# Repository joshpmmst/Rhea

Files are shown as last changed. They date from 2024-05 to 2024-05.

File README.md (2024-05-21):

# Rhea: An open-source table tennis ball launcher robot for multiball training

<picture>
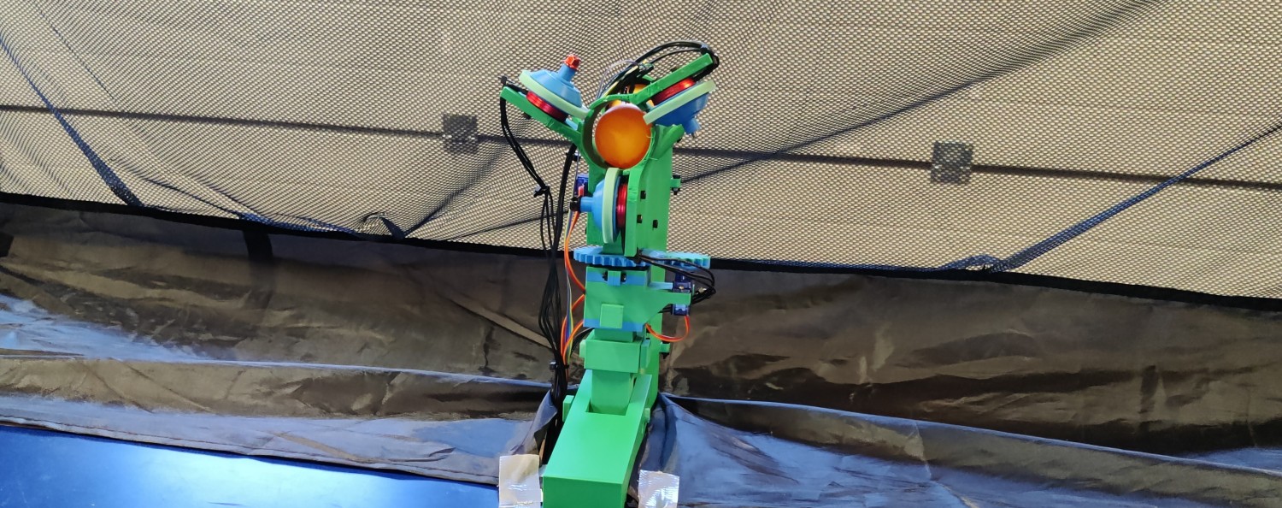
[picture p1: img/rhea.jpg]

</picture>

## About

Rhea is an open-source table tennis ball launcher intended for multiball training.
Rhea is manufacturable with common hobbyist tools and comprises of readily available materials and components.

## Contents
  - [3D printing and assembly instructions](printing-and-assembly)
  - [Bill of Materials](bill-of-materials)
  - [3D models](models)
  - [Firmware](firmware)
  - [User software](software)

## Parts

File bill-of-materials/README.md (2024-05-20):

## Bill of Materials

All prices as of 2024-05-20.

Component | Quantity | Cost (EUR)
---|---|---
TowerPro SG90 | 2 | [4.94](https://nettigo.eu/products/sg90-small-hobby-servo)
Parallax Continuous Rotation Servo #900-00008 | 1 | [18.55](https://www.mouser.ee/ProductDetail/Parallax/900-00008?qs=Ok6sVjDQtqYSeReZa9t%252Bvg%3D%3D)
Racerstar BR2205S 2300KV | 3 | [38.16](https://www.banggood.com/Racerstar-Racing-Edition-2205-BR2205-2300KV-2-4S-Brushless-Motor-Red-for-220-250-RC-Drone-FPV-Racing-p-1065661.html?ID=521309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)
Racerstar MS Series 35A | 3 | [51.00](https://www.ariesrc.gr/en/speed-controller/16240-racerstar-ms-series-35a-esc-blhelis-opto-2-4s-supports-dshot600-for-rc-drone-fpv-racing-multi-rotor.html) (a)
Zhermack Elite Double 22 polysiloxane | 20 ml | [0.76](https://edenta.eu/et/proteesitarvikud/elite-double-22-normal-1-kg-1-kg) (b)
PLA filament | 1115 g | [18.46](https://esun3dstore.com/collections/pla/products/esun-epla-ss-1-75mm-3d-filament-1kg)
DOIT ESP32 DevKit V1 | 1 | [4.73](https://www.aliexpress.com/item/1005005988314674.html)
Vishay TCRT5000 | 2 | [3.96](https://ee.farnell.com/vishay/tcrt5000/sensor-optical-transistor-o-p/dp/1470066)
TIGER Power Supplies TP1024 | 1 | [14.31](https://ee.farnell.com/tiger-power-supplies/tp1024/power-supply-ac-dc-1o-p-5a-12v/dp/4132955)
Wurth Elektronik 694106402002 | 1 | [1.24](https://ee.farnell.com/wurth-elektronik/694101308002/connector-power-entry-jack-2a/dp/2472139)
OKYSTAR OKY3501-1 | 1 | [5.08](https://www.teval.ee/en/shop/product/oky3501-1-converter-step-down-uout-5v-uin-624v-3a-94-26-4x15mm-236530) (c)
Quarter sized protoboard | 1 | [2.02](https://www.aliexpress.com/item/4000372698705.html)
WAGO 221 3-conductor | 3 | [2.07](https://solislux.eu/en/product/221-613-compact-splicing-connectors;-3-conductor-connector;-with-operating-levers;-max-ambient-operating-temp--85-%C2%B0c/)
WAGO 221 5-conductor | 1 | [1.16](https://solislux.eu/en/product/221-615-compact-splicing-connectors;-5-conductor-connector;-with-operating-levers;-max-ambient-operating-temp--85-%C2%B0c/)
470 Ohm resistor | 2 | 0.02 (d)
10k Ohm resistor | 2 | 0.02 (d)
22 AWG four wire ribbon cable | 1 m | [1.28](https://www.aliexpress.com/item/32956565616.htm)
18 AWG wire | 3 m | [2.38](https://ee.farnell.com/pro-power/pp001187/tri-rated-wire-1mm2-black-1m/dp/2528083)
14 AWG wire | 2 m | [3.35](https://ee.farnell.com/pro-power/pp001189/tri-rated-wire-2-5mm2-black-1m/dp/2528085)
10 cm male to female jumper wires | 20 | [0.97](https://www.aliexpress.com/item/4000203371860.html)
15x32x9 metal ball bearing 6002/C3 SKF | 1 | [5.13](https://www.alas-kuul.ee/radiaalkuullaager-6002-c3-skf)
M3 bolts and nuts | 1 | 1.21 (e)
**TOTAL** | | **180.80**

(a) - Can be substitituded with more recent ESCs:
[Simonk 10A](https://www.aliexpress.com/item/1005005032261137.html) (14.58 EUR for 3 pieces).

(b) - Can be substituted, recommended Shore A hardness of 20-25. [Polistep PLS-525](https://polistep.lv/en/two-component-silicone/tproduct/282059541-460415774771-moulding-silicone-on-tin-catalyst-pls-52) (0.36 EUR for 20 ml)

(c) - Can be substituted. [LM2596 DC-DC module](https://www.aliexpress.com/item/1005004904872120.html) (1.57 EUR per piece)

(d) - The resistors were used from a 300 piece kit costing [2.28](https://www.aliexpress.com/item/1005006209050774.html) EUR.

(e) - M3 bolts and nuts were used from a 300 piece kit costing [6.48](https://www.aliexpress.com/item/33022099174.html) EUR. The following lists all M3 bolts and nuts used.

Component | Quantity
---|---
M3x8 bolt | 14
M3x12 bolt | 22
M3x16 bolt | 4
M3x20 bolt | 4
M3 nut | 12

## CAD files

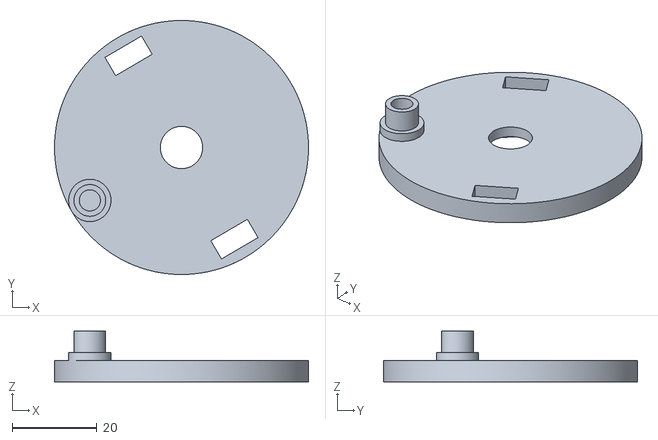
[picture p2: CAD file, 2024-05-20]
models/Ball Pusher/Crank.stl
60.0 x 60.0 x 12.0

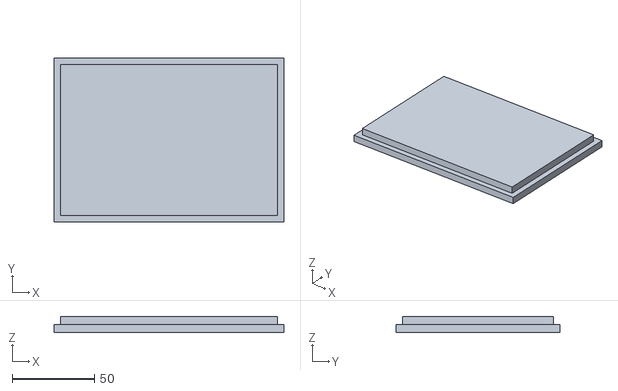
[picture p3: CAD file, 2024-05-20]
models/Enclosure/Enclosure lid.stl
140.0 x 100.0 x 10.0

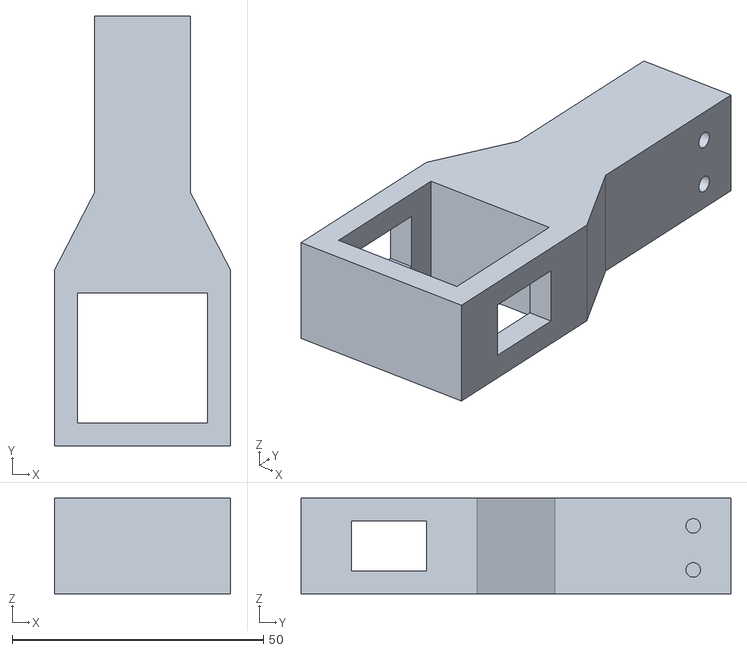
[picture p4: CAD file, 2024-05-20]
models/Fixture/Pusher and Pipe connector.stl
35.0 x 85.5 x 19.0

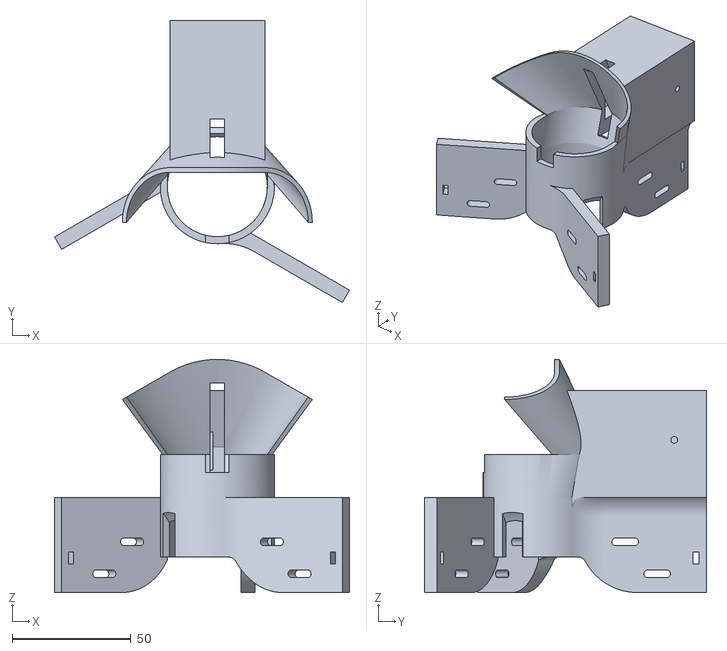
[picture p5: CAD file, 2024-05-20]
models/Launch Unit/Launch Unit.stl
124.0 x 118.6 x 98.0

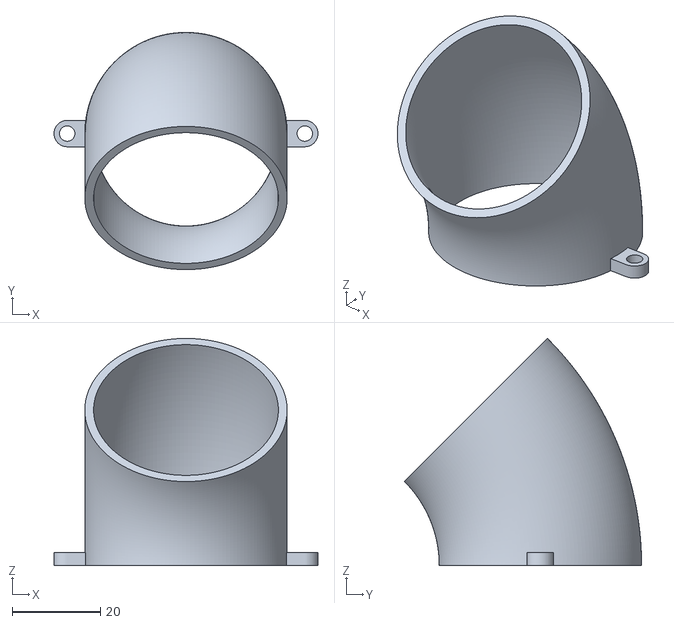
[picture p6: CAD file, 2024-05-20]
models/Pipe/Angled connector pipe 2.stl
60.0 x 53.9 x 51.6

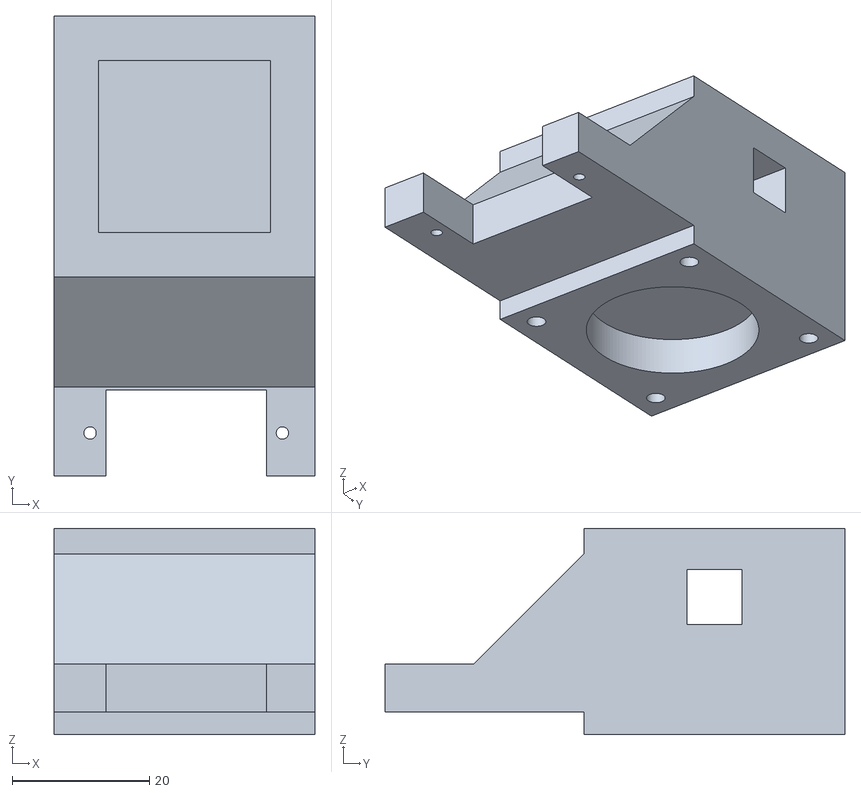
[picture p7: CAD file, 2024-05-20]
models/Pivot Mechanism/Housing.stl
38.0 x 67.0 x 30.0

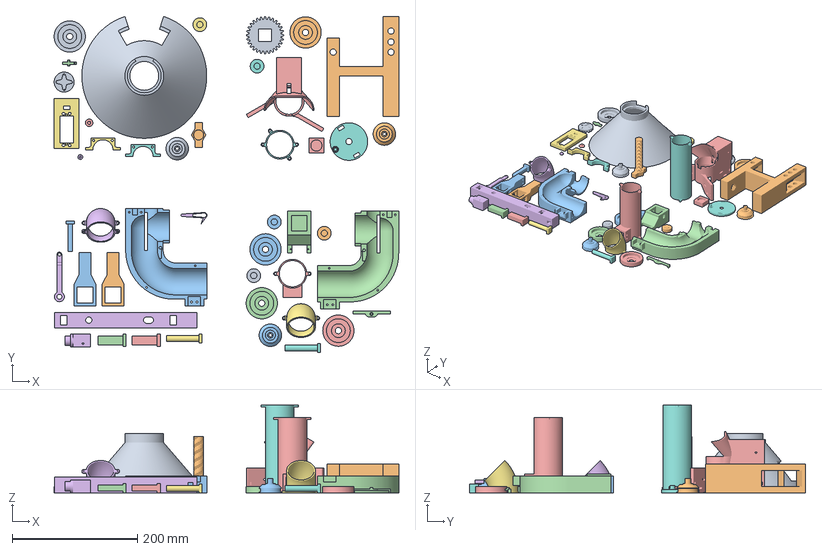
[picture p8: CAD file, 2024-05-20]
models/Plates.3mf
551.2 x 537.2 x 140.0 mm
Funnel.stl
Clamp.stl
Housing 2.stl
Housing 1.stl
Launch Unit.stl
Rod.stl
Parallax servo holder.stl
Crank.stl
Driven gear.stl
Pusher and Pipe connector.stl x 2
Housing.stl
Straight connector pipe top.stl
Angled connector pipe 1.stl
Angled connector pipe 2.stl
Straight connector pipe bottom.stl
Traction wheel mould outer.stl x 5
Connecting rod.stl
Bearing housing.stl x 2
Motor guard.stl x 3
Rectangular dowel.stl x 2
Shaft.stl
Round dowel.stl x 2
Driver gear.stl
Bolt.stl
Square dowel.stl
Piston.stl
Bolt pad.stl
Servo hook.stl
Traction wheel mould inner.stl x 5
Ball stopper.stl
Crank retaining pin.stl
Piston retaining pin.stl

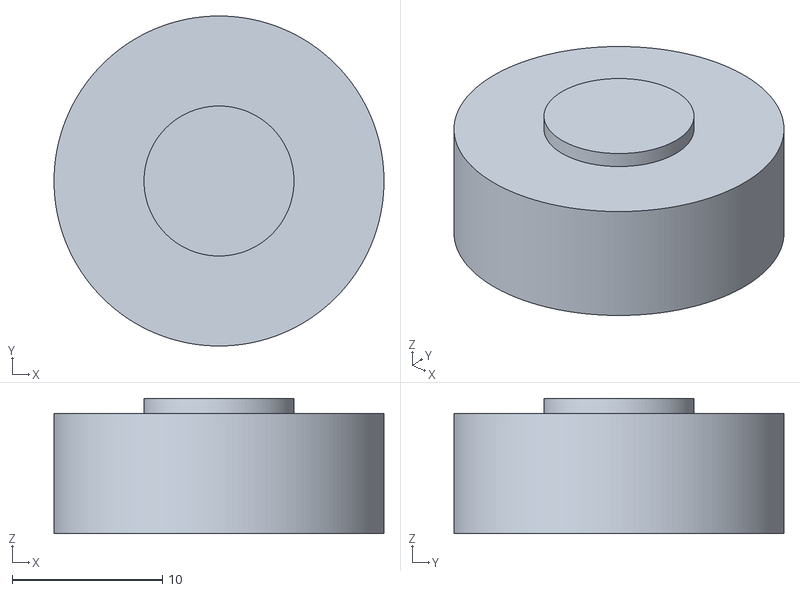
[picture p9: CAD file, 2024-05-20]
models/Traction wheel mould/Traction wheel mould inner.stl
22.0 x 22.0 x 9.00

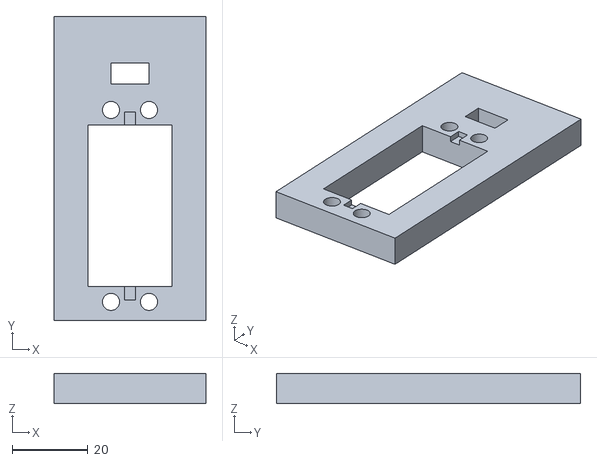
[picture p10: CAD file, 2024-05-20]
models/Ball Pusher/Parallax servo holder.stl
40.0 x 80.0 x 8.00

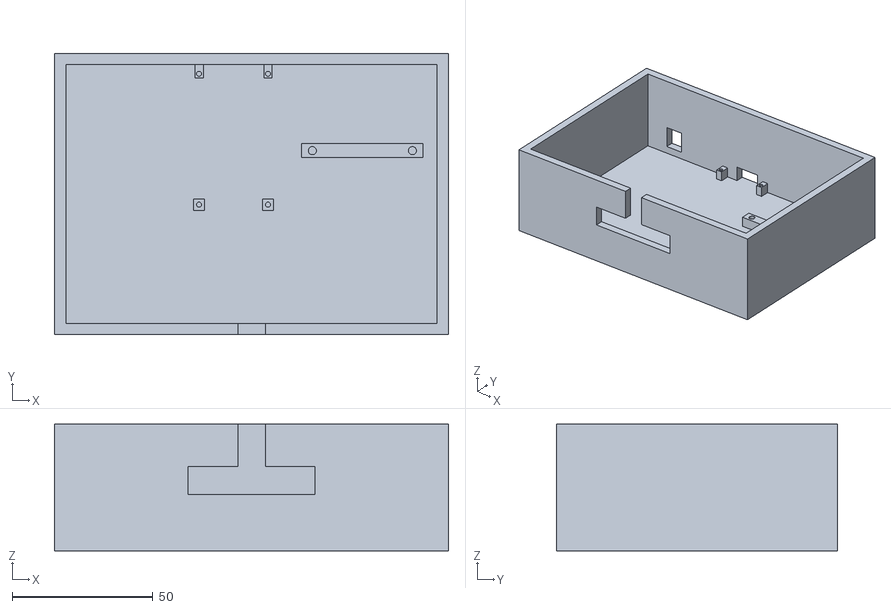
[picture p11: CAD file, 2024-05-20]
models/Enclosure/Enclosure.stl
140.0 x 100.0 x 45.0

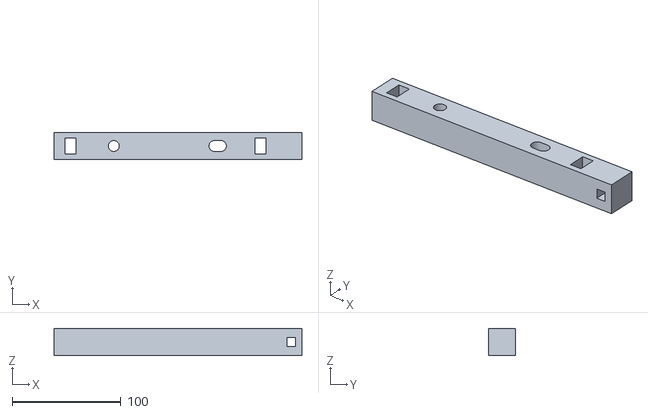
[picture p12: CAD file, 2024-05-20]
models/Fixture/Rod.stl
228.0 x 25.0 x 25.0

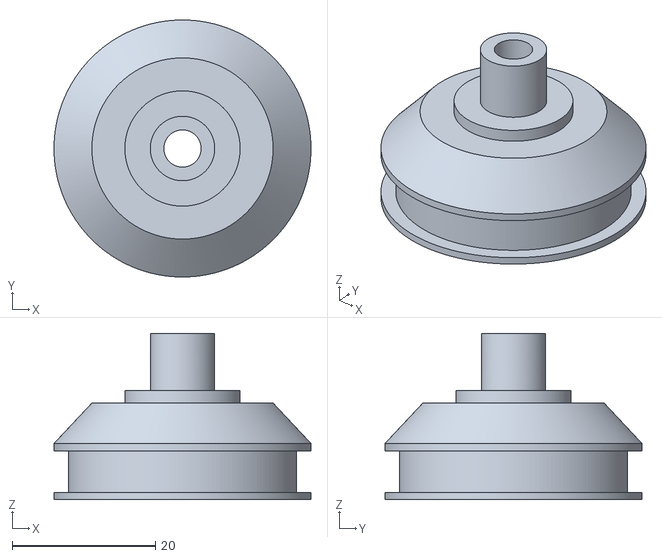
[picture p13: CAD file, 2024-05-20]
models/Launch Unit/Motor guard.stl
35.9 x 35.9 x 23.2

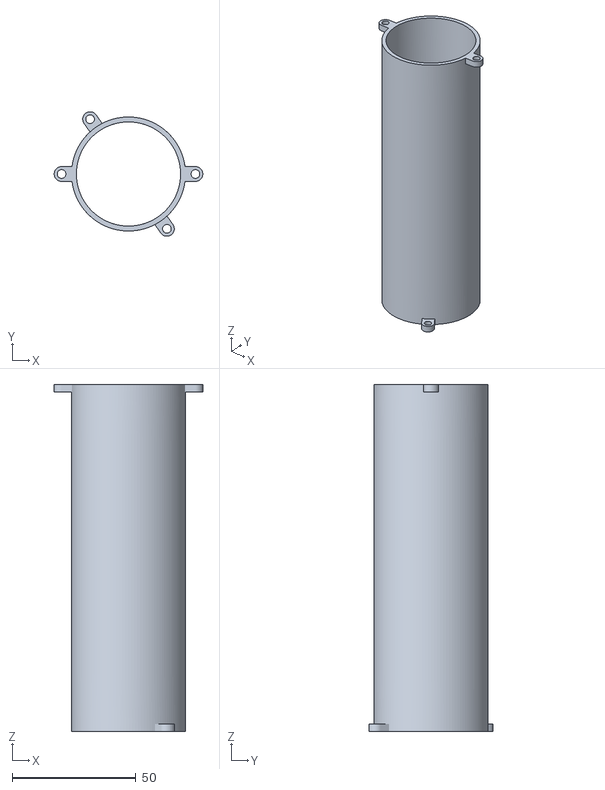
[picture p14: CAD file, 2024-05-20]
models/Pipe/Straight connector pipe bottom.stl
60.0 x 50.2 x 140.0

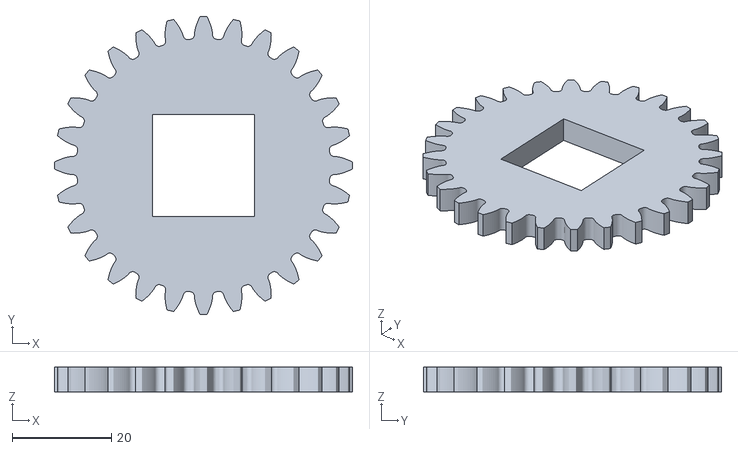
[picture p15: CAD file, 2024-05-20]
models/Pivot Mechanism/Driven gear.stl
60.0 x 60.0 x 5.00

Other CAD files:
models/Traction wheel mould/Traction wheel mould outer.stl
models/Ball Pusher/Piston retaining pin.stl
models/Fixture/Clamp.stl
models/Launch Unit/Servo hook.stl
models/Ball Pusher/Ball stopper.stl
models/Ball Pusher/Connecting rod.stl
models/Ball Pusher/Crank retaining pin.stl
models/Ball Pusher/Funnel.stl
models/Ball Pusher/Housing 1.stl
models/Ball Pusher/Housing 2.stl
models/Ball Pusher/Piston.stl
models/Fixture/Bolt pad.stl
models/Fixture/Bolt.stl
models/Fixture/Rectangular dowel.stl
models/Fixture/Round dowel.stl
models/Fixture/Square dowel.stl
models/Pipe/Angled connector pipe 1.stl
models/Pipe/Straight connector pipe top.stl
models/Pivot Mechanism/Bearing housing.stl
models/Pivot Mechanism/Driver gear.stl
models/Pivot Mechanism/Shaft.stl

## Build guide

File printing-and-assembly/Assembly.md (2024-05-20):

# Assembly instructions

## Ball Pusher

1. Solder four ribbon cable wires to the TCRT5000 sensor and glue it to the `Parallax servo holder`.

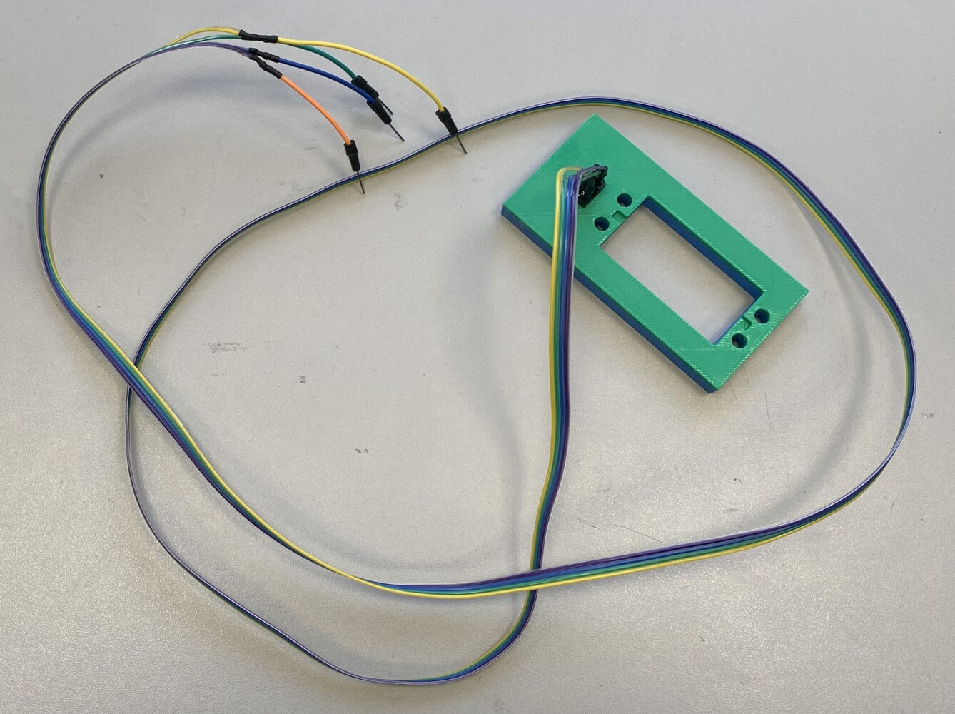
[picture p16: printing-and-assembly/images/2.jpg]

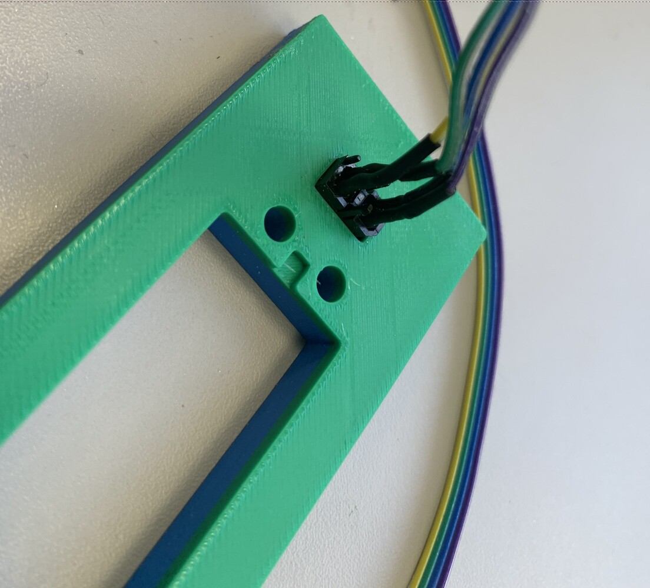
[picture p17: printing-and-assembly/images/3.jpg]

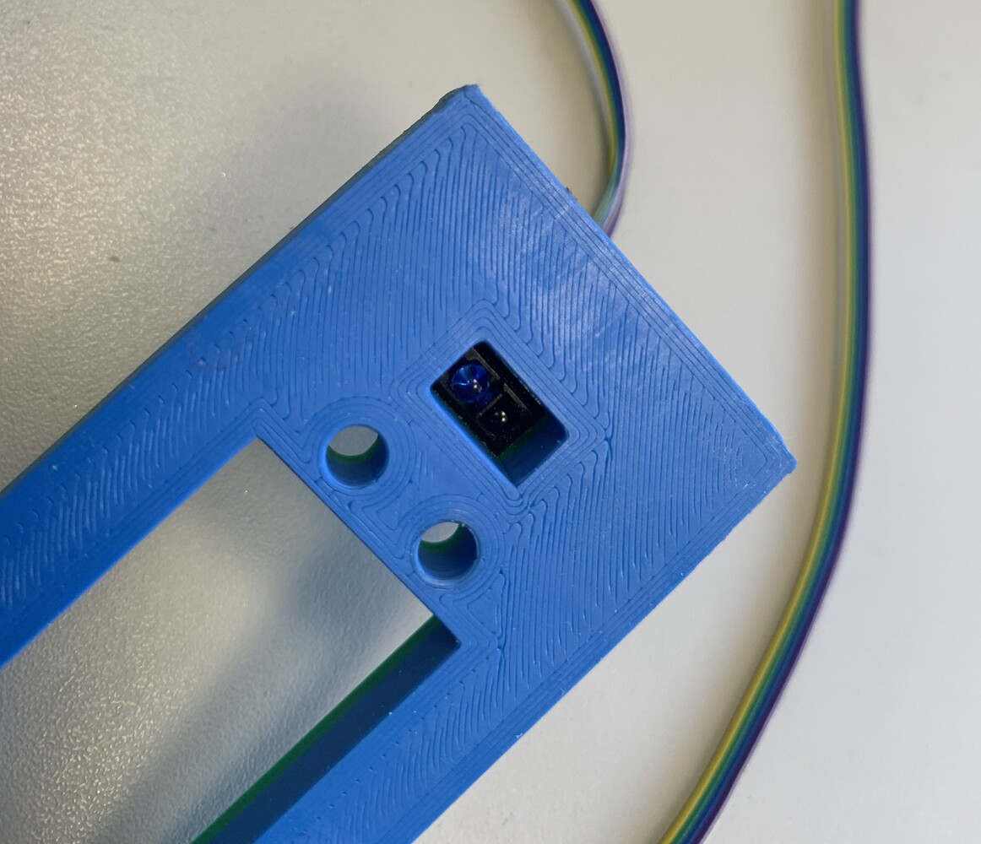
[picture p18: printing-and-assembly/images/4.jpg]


2. Mount the Parallax continuous servomotor to the `Parallax servo holder` using four M3x16 bolts with nuts. Two bolts are sufficient.

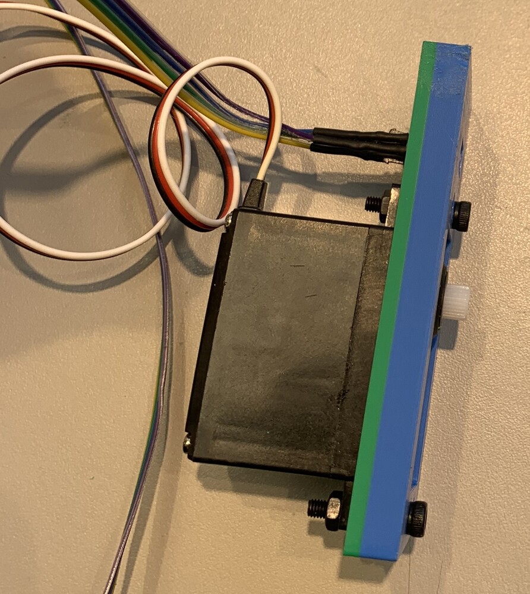
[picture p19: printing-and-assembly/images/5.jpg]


3. Pressure fit the cross-shaped connector provided with the Parallax continous servo into the `Crank`. Use glue if the fit is loose.

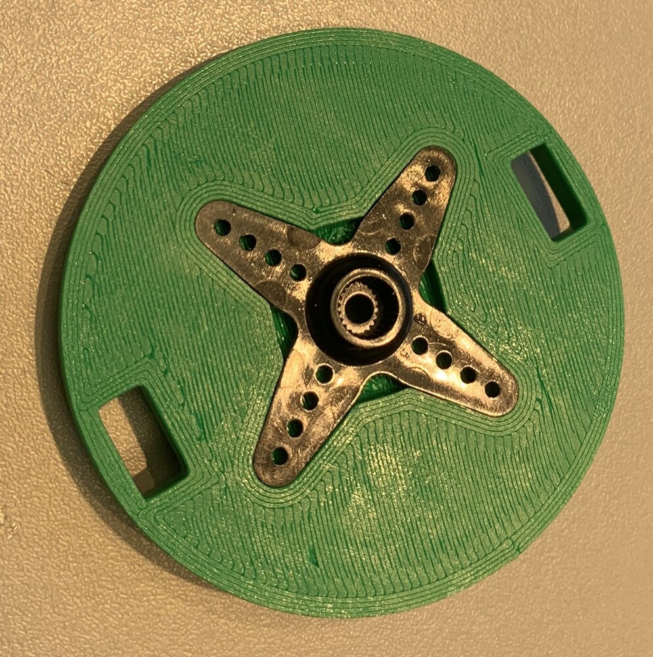
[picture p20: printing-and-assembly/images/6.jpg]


4. Secure the cross connector and the `Crank` to the servomotor using the screw provided with the servomotor.

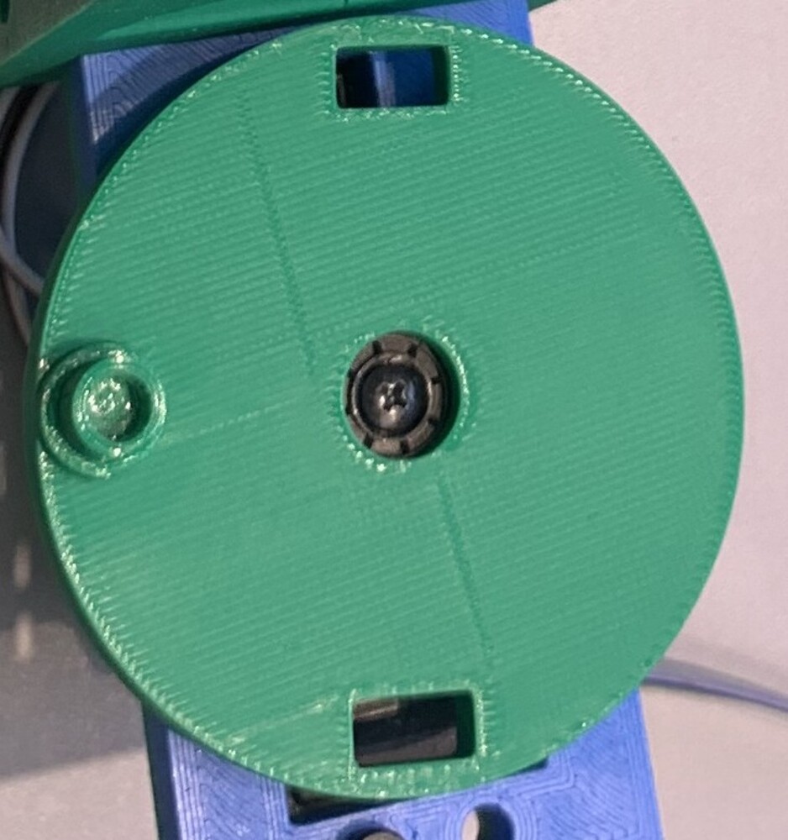
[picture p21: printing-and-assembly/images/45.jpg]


5. Pressure fit the `Parallax servo holder` into `Housing 1`. Place the `Ball stopper` into `Housing 1` as indicated by the red square.

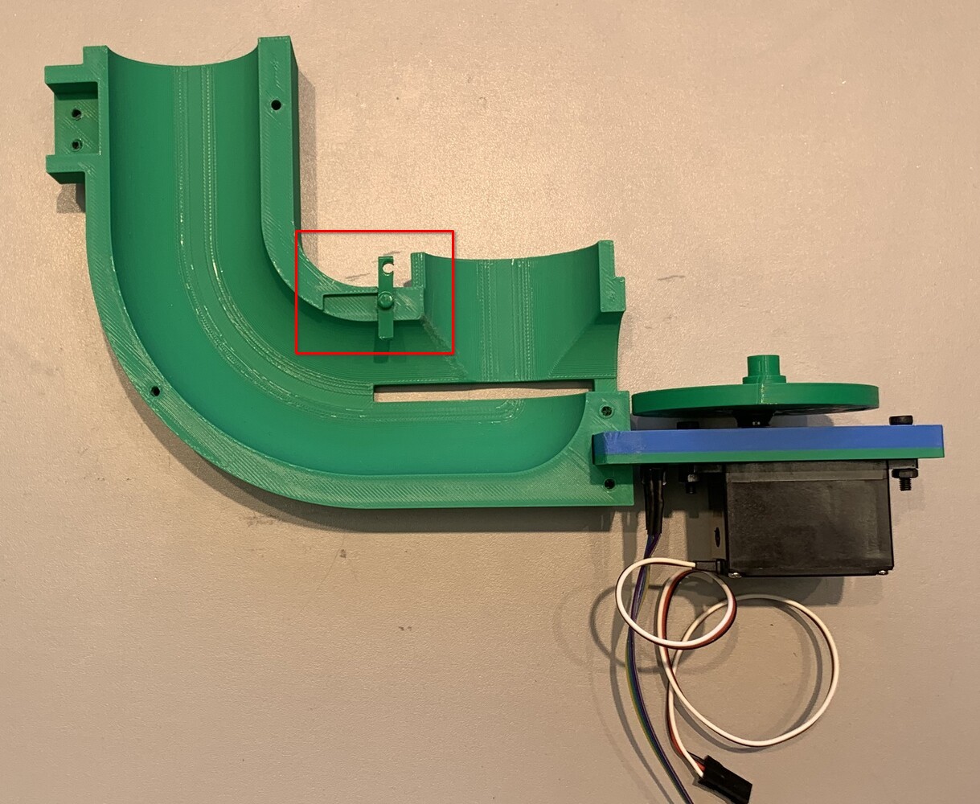
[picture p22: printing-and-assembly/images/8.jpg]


6. Slide the `Piston` sideways into `Housing 1`.

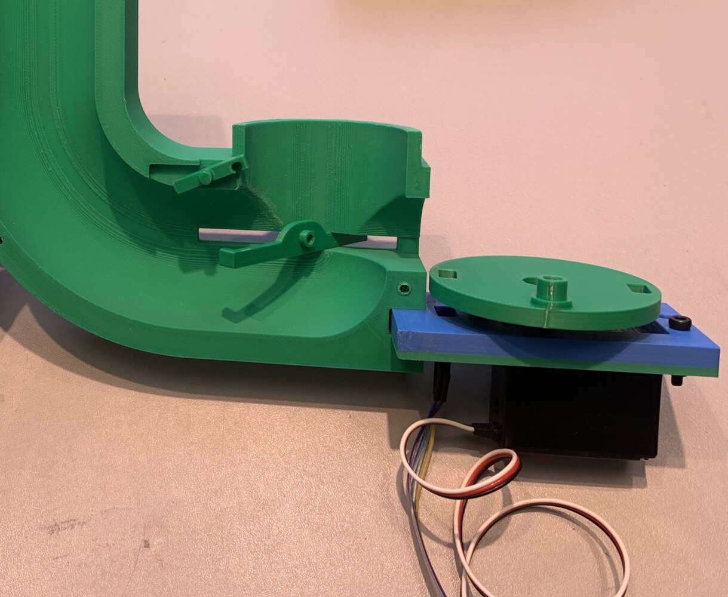
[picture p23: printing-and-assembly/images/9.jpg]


7. Attach `Housing 2` to `Housing 1`.

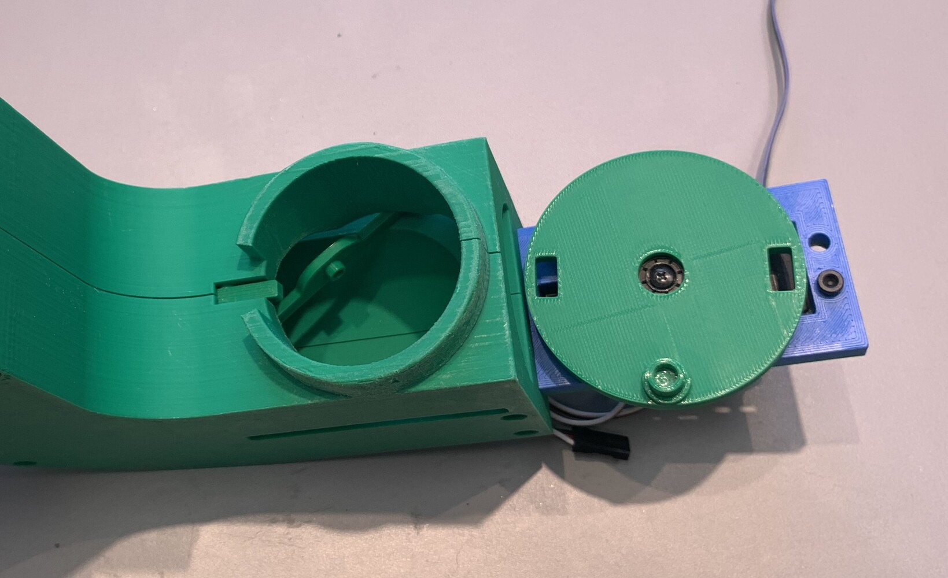
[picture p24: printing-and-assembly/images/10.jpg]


8. Twist the `Piston` counterclockwise so it is parallel to the sliding surface.

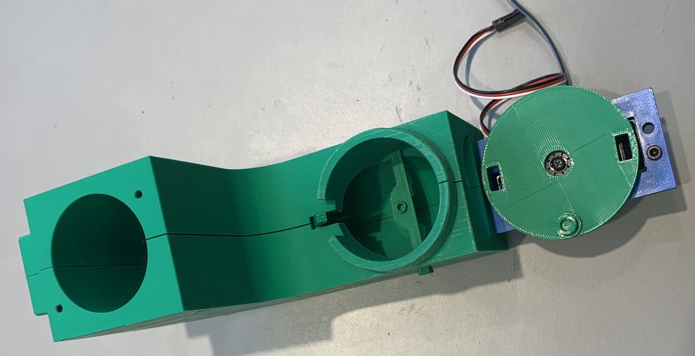
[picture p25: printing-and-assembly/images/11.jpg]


9. Attach the `Connecting rod` to the `Crank` and `Piston`.

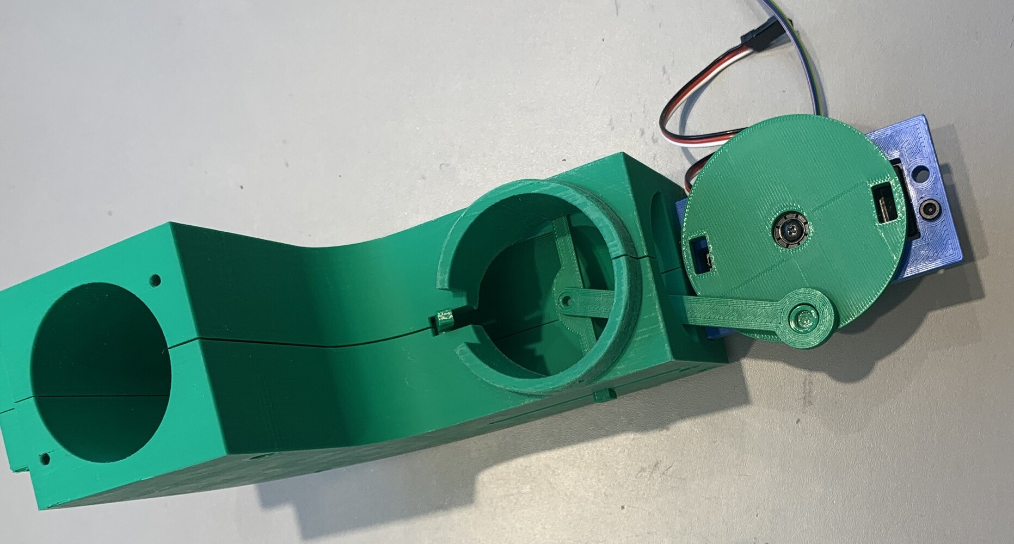
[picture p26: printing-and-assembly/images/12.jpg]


10. Attach the `Crank retaining pin` to the `Crank` and the `Piston retaining pin` to the `Piston`.

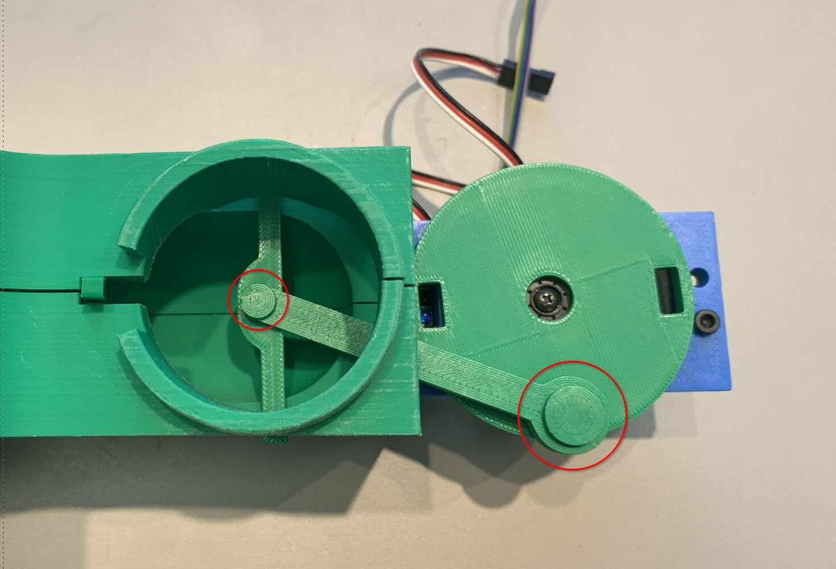
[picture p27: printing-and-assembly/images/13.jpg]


11. Secure `Housing 1` and `Housing 2` together using four M3x20 bolts. Nuts are not required as the holes' inner diameter is smaller inside.

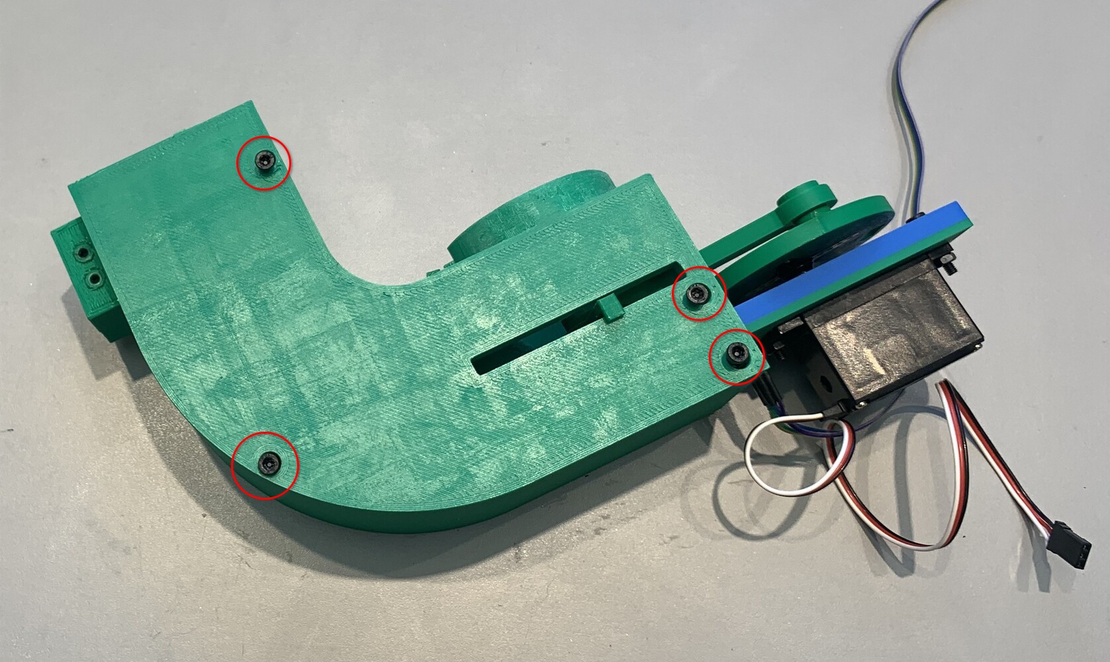
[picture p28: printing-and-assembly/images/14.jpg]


12. Attach a rubber band to hold the `Ball stopper` upright.

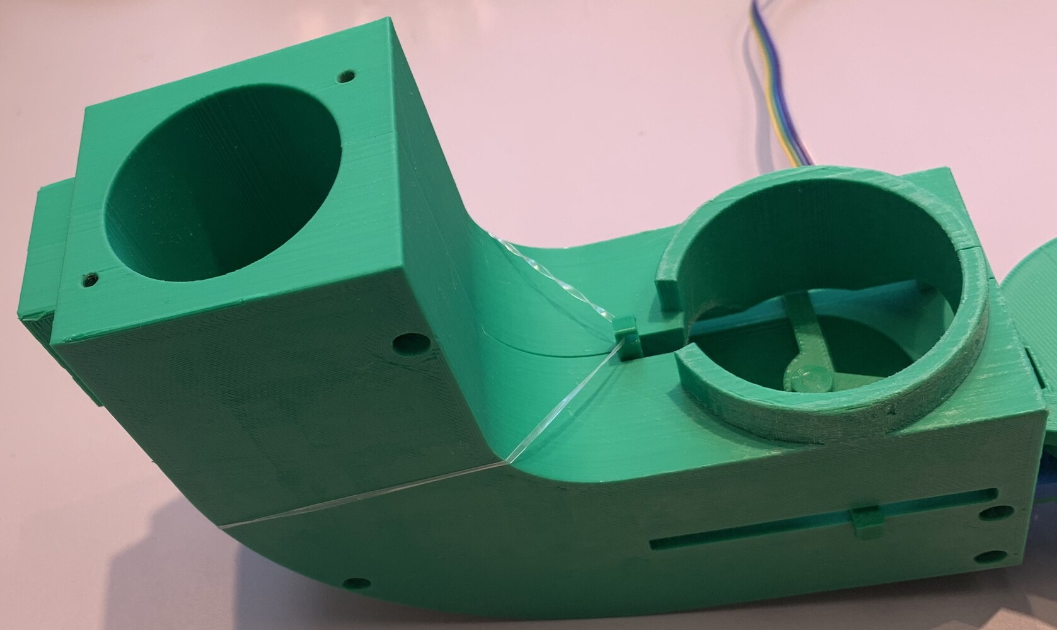
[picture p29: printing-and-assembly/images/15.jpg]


## Pipe

1. Secure `Angled connector pipe 1` and `Angled connector pipe 2` together using two M3x12 bolts and nuts on both sides.

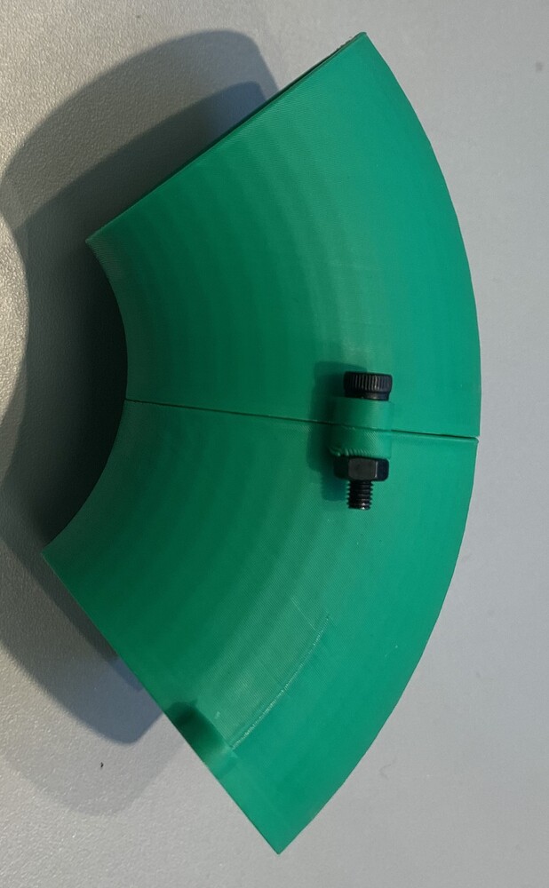
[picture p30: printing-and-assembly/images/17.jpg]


2. Secure `Straight connector pipe top` and `Angled connector pipe 1` together using two M3x12 bolts and nuts on both sides.

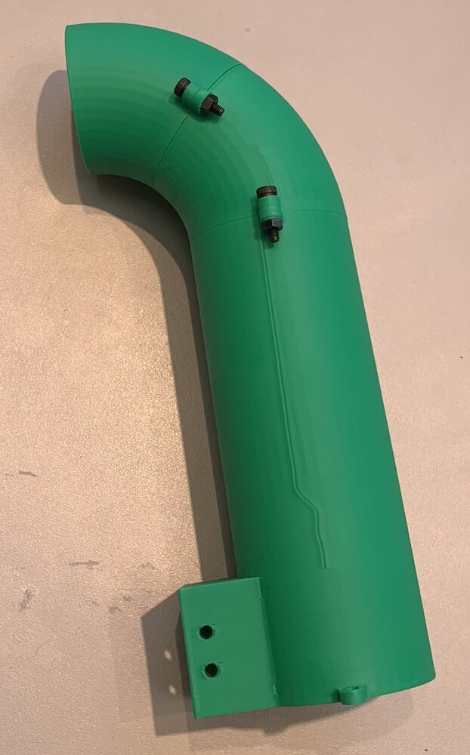
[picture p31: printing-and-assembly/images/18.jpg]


3. Secure `Straight connector pipe top` and `Straight connector pipe bottom` together using two M3x12 bolts and nuts on both sides.

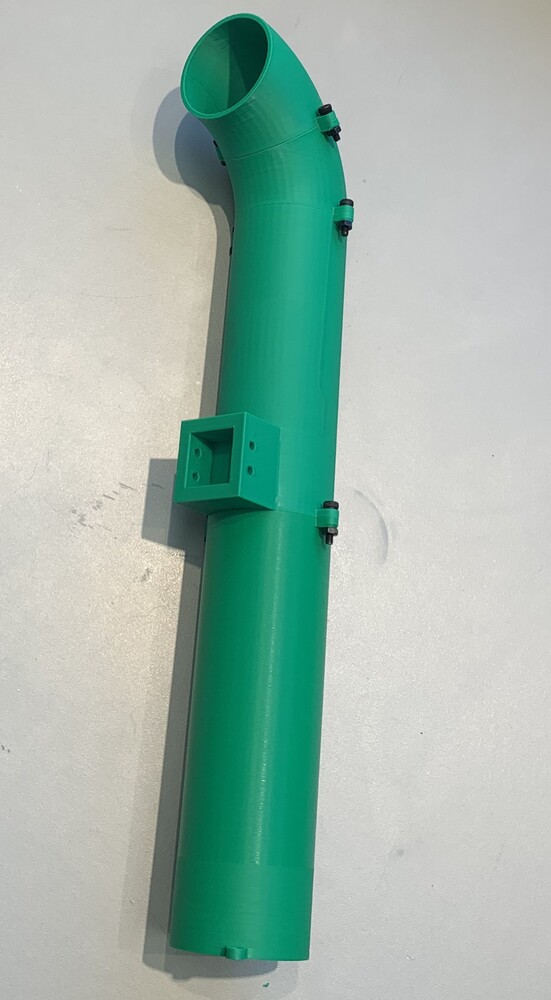
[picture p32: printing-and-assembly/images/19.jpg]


## Launch Unit

1. Make three traction wheels with `Traction wheel mould inner` and `Traction wheel mould outer` using polysiloxane. I recommend Shore 20-25 A hardness polysiloxane.

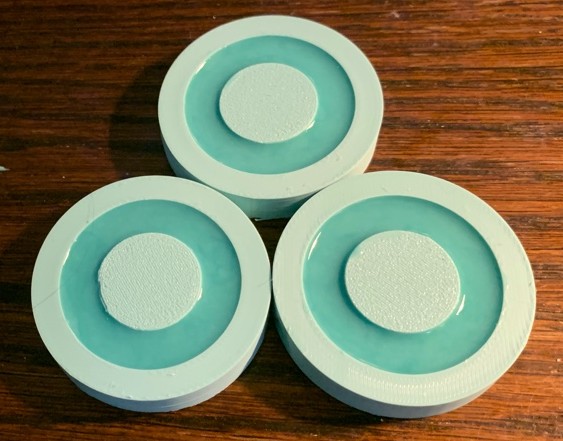
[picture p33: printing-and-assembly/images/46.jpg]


2. For each of the three BLDC motors: attach the `Motor guard`, stretch polysiloxane traction wheel around the `Motor guard`, and secure it using flange nut provided with the motor.

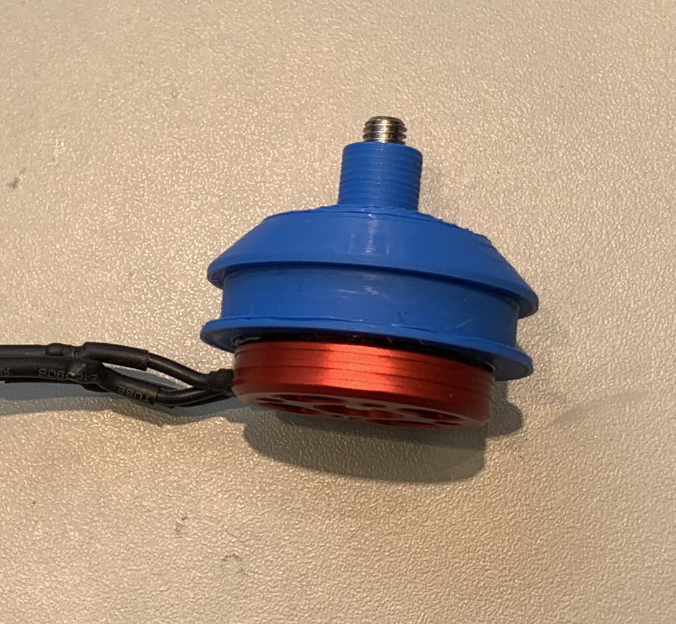
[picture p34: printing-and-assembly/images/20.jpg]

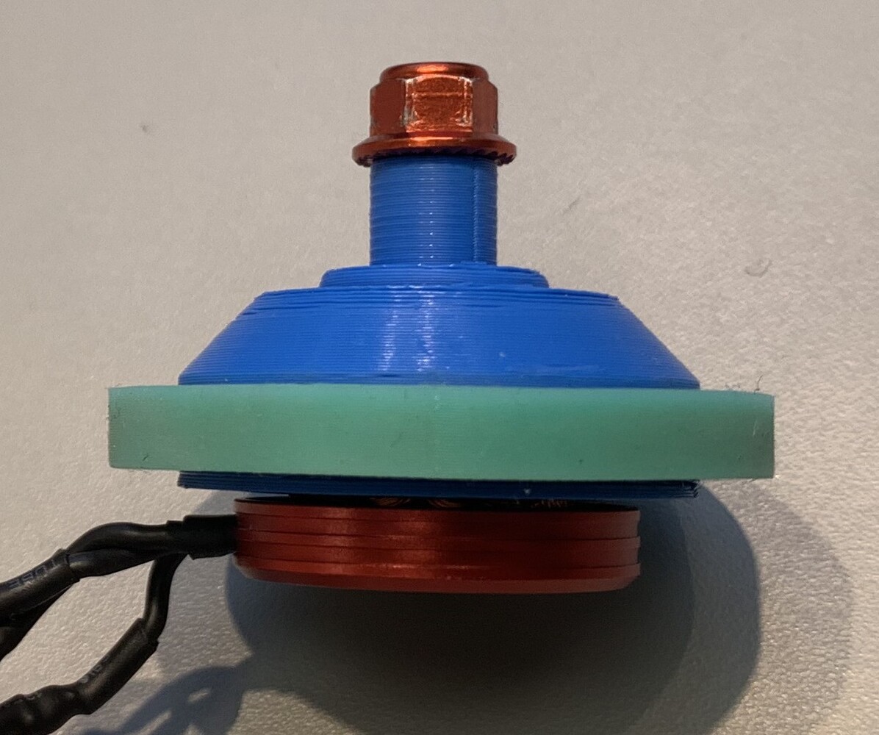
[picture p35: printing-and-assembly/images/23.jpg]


3. Pressure fit the arm-shaped connector that came with the TG90 servomotor into the `Servo hook`. Use glue if the fit is loose.

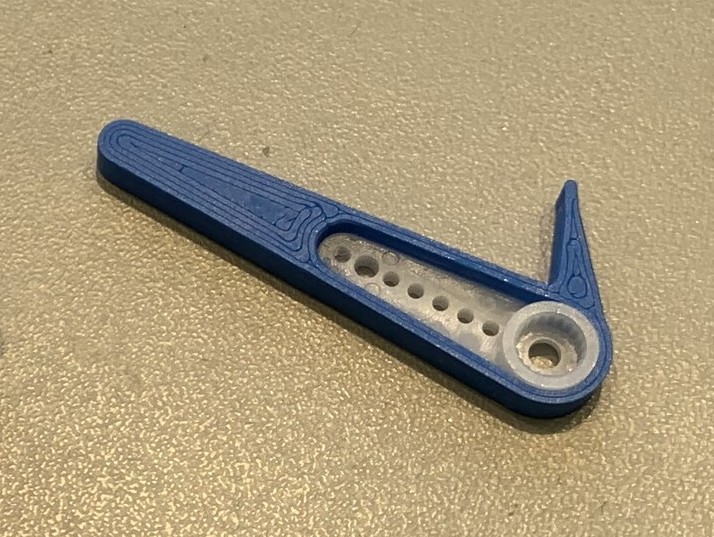
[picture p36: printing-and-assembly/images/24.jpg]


4. Mount the servomotor into the `Launch Unit` while connecting the servomotor to the arm-shaped connector. Secure it using two screws provided with the servomotor. **Note:** I recommend connecting the servomotor and `Servo hook` later if the position of the servomotor is unknown. 

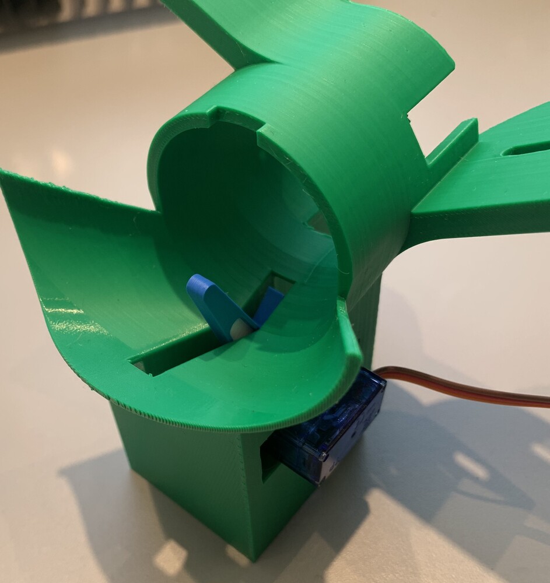
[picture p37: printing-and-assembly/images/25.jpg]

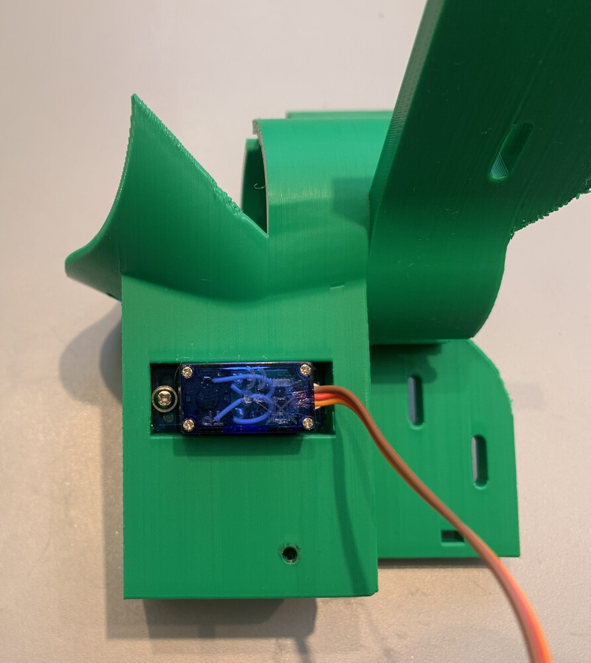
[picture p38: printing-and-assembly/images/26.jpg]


5. Attach the three BLDC motors to the `Launch Unit` using six M3x8 bolts. Adjust the pinching distance as necessary. I recommend trying to minimise the pinching distance as much as possible with all three traction wheels still making contact with a table tennis ball.

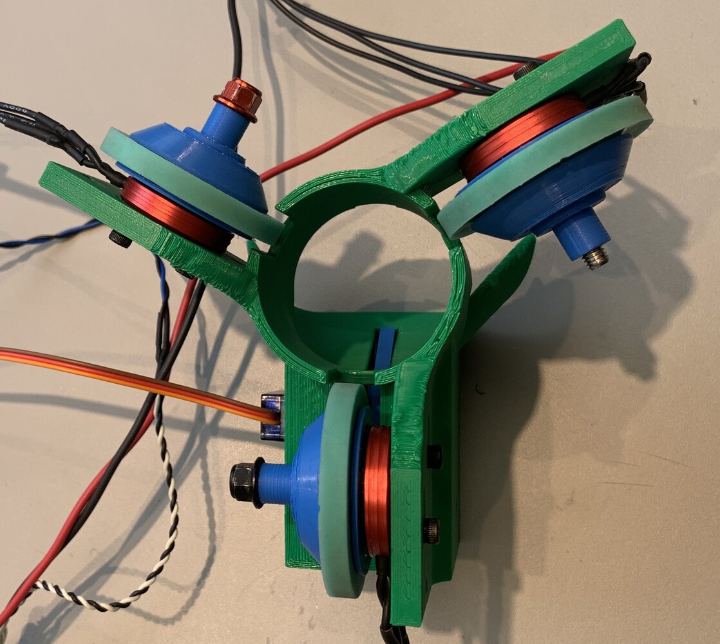
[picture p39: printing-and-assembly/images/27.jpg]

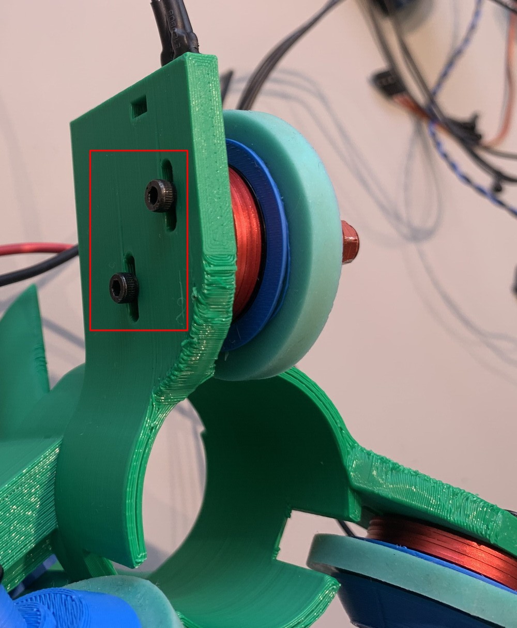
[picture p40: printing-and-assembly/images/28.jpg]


6. Solder four ribbon cable wires to the TCRT5000 sensor and glue it to the `Launch Unit`.

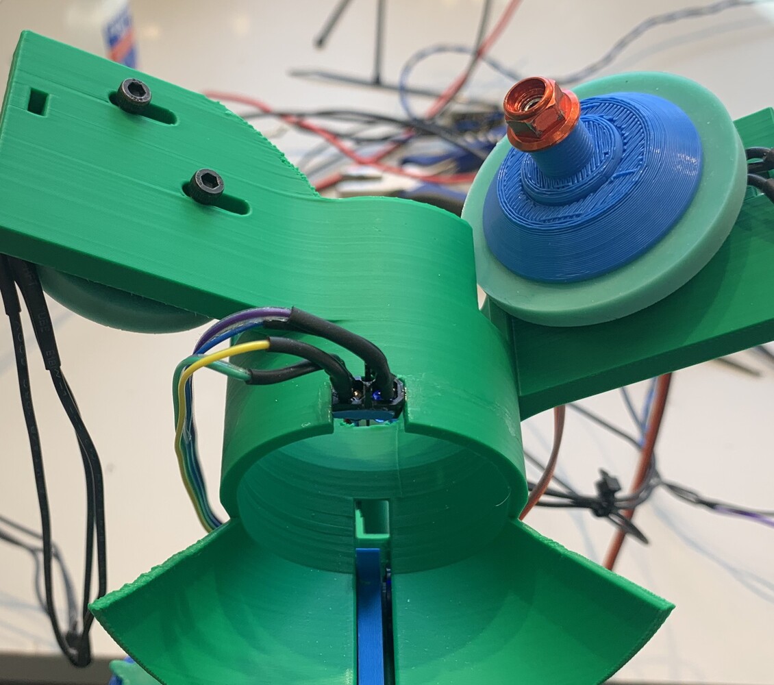
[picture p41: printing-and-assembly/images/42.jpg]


## Pivot Mechanism

The assembly images show the Pivot Mechanism already connected to the Fixture but this is not required.

1. Place two `Bearing housing` on the `Housing` and lightly screw in four M3x12 bolts into the `Housing` but do not tighten them yet.

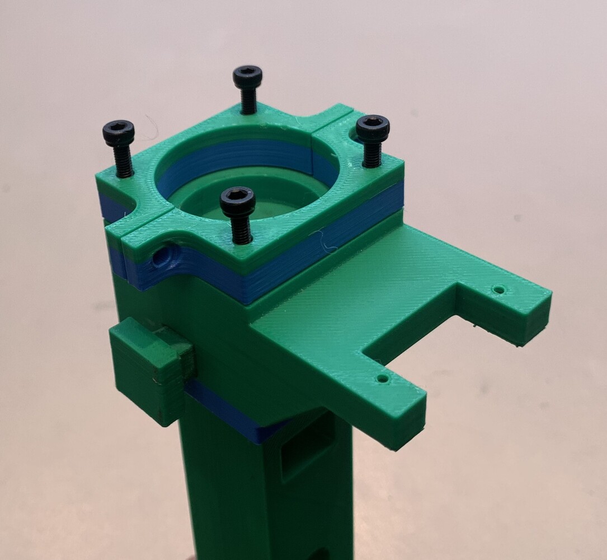
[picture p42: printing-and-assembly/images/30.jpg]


2. Secure the servomotor to the `Housing` using the provided screws and mount the provided cross-shaped connector to it.

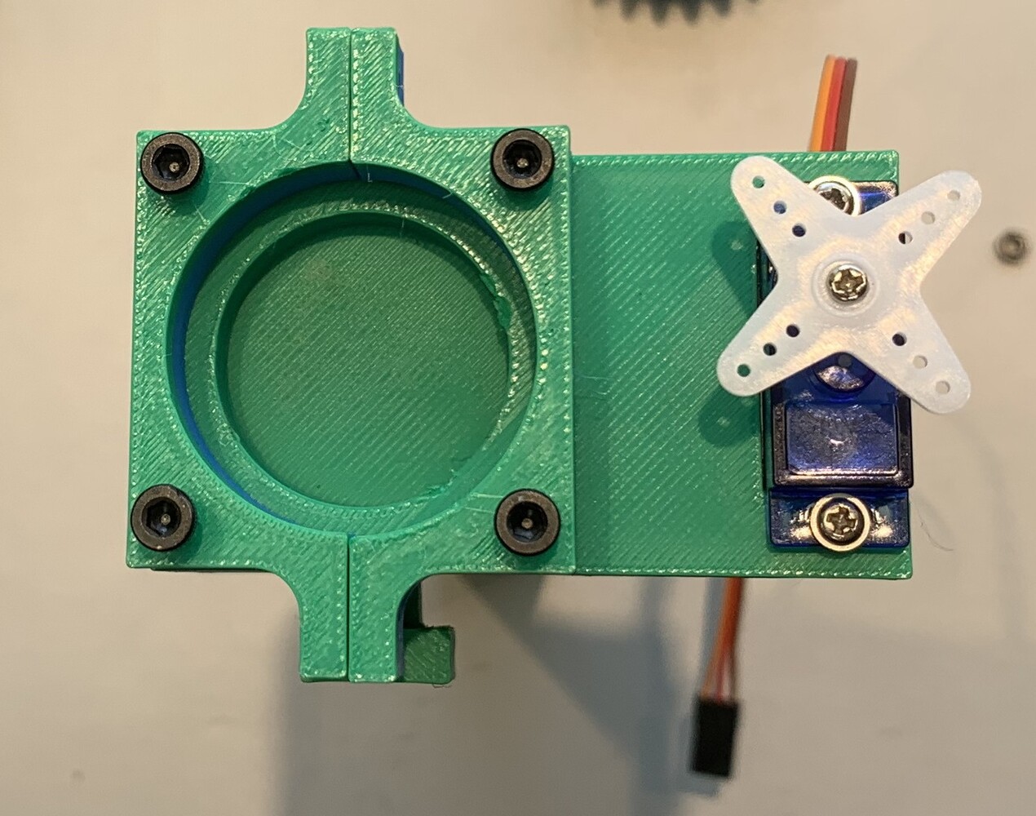
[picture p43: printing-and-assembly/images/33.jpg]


3. Fit the 15x32x9 metal ball bearing between the two `Bearing housing`s and tighten them together using two M3x12 bolts and nuts. Tighten the four M3x12 bolts placed in step 1. Pressure fit the  `Shaft` into the ball bearing. Pressure fit the `Driver gear` into the arm-shaped cross of the servomotor. **Note:** I recommend pressure fitting the `Driven gear` into the `Shaft` later as the servomotor's initial position is unknown.

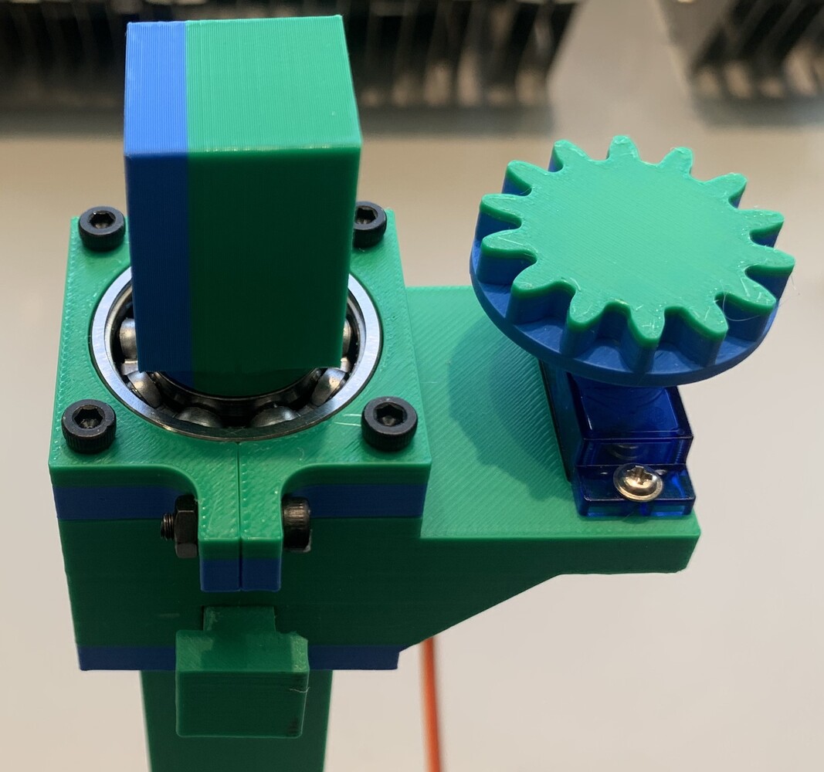
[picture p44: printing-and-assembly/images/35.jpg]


## Fixture

1.
    1. Slide and secure the first `Pusher and Pipe connector` into the `Rod` using the first `Rectangular dowel`.
    2. Slide and secure the Pivot Mechanism into the `Rod` using the `Square dowel`.
    3. Slide the `Rod` into the `Clamp` and secure it using two `Round dowel`s. 
    4. Slide and secure the first `Pusher and Pipe connector` into the `Rod` using the first `Rectangular dowel`.
    5. Turn the `Bolt` into the `Clamp`. The `Bolt pad` can be used between the `Bolt` and a table's underside when mounting.

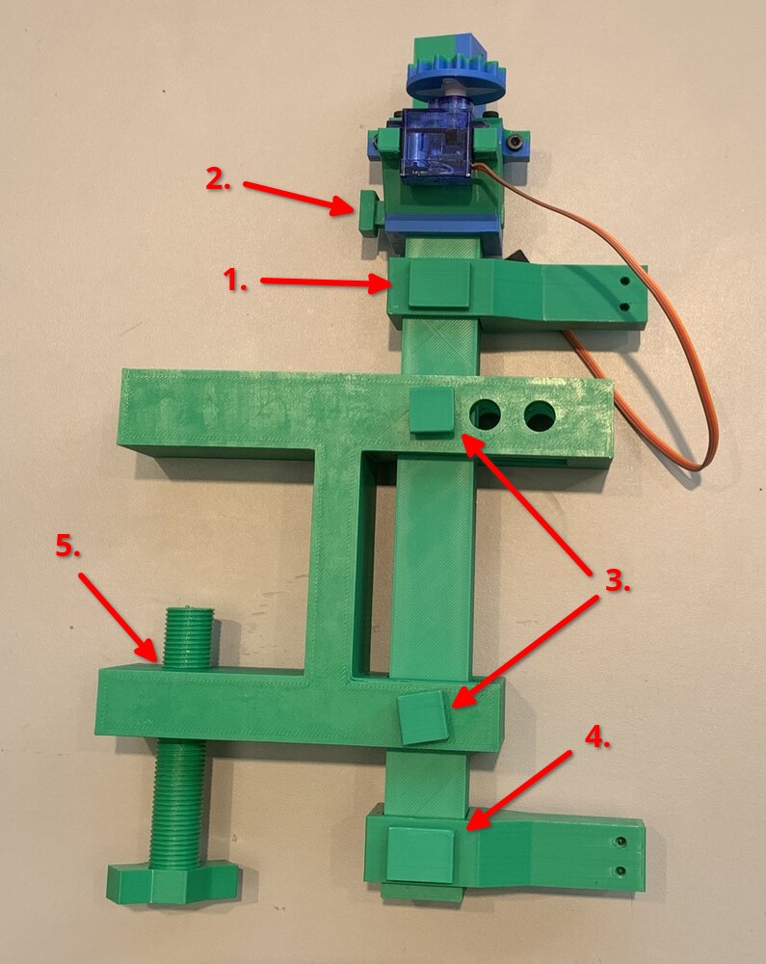
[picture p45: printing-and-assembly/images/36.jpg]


2. Secure the Ball Pusher to the Fixture using four (one side depicted) M3x12 bolts.

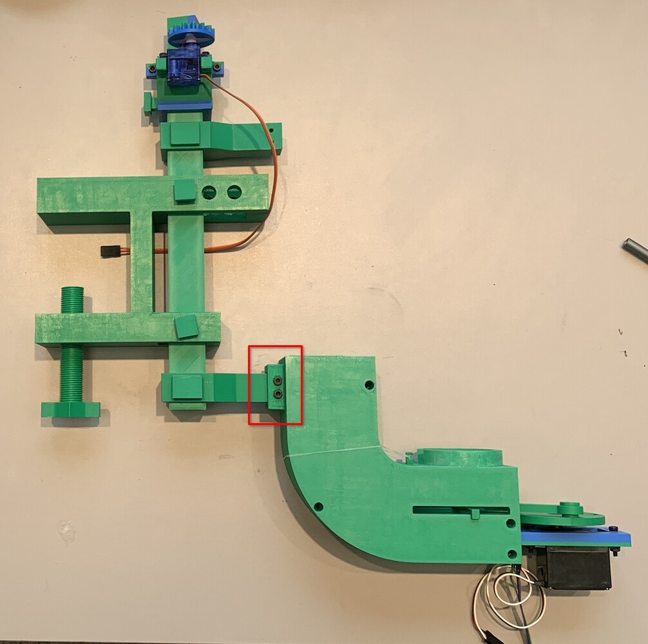
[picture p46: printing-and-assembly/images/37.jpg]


3. Secure the Launch Unit to the Pivot Mechanism's `Shaft` using two M3x12 bolts. **Note:** Before securing the Launch Unit, find the zero position of the Pivot Mechanism's servomotor by powering the robot on. The firmware rotates the servomotor to its midway position (0 degree yaw angle) on startup. Afterwards, pressure fit the Pivot Mechanism's `Driven gear` into the `Shaft` and then secure the Launch Unit.

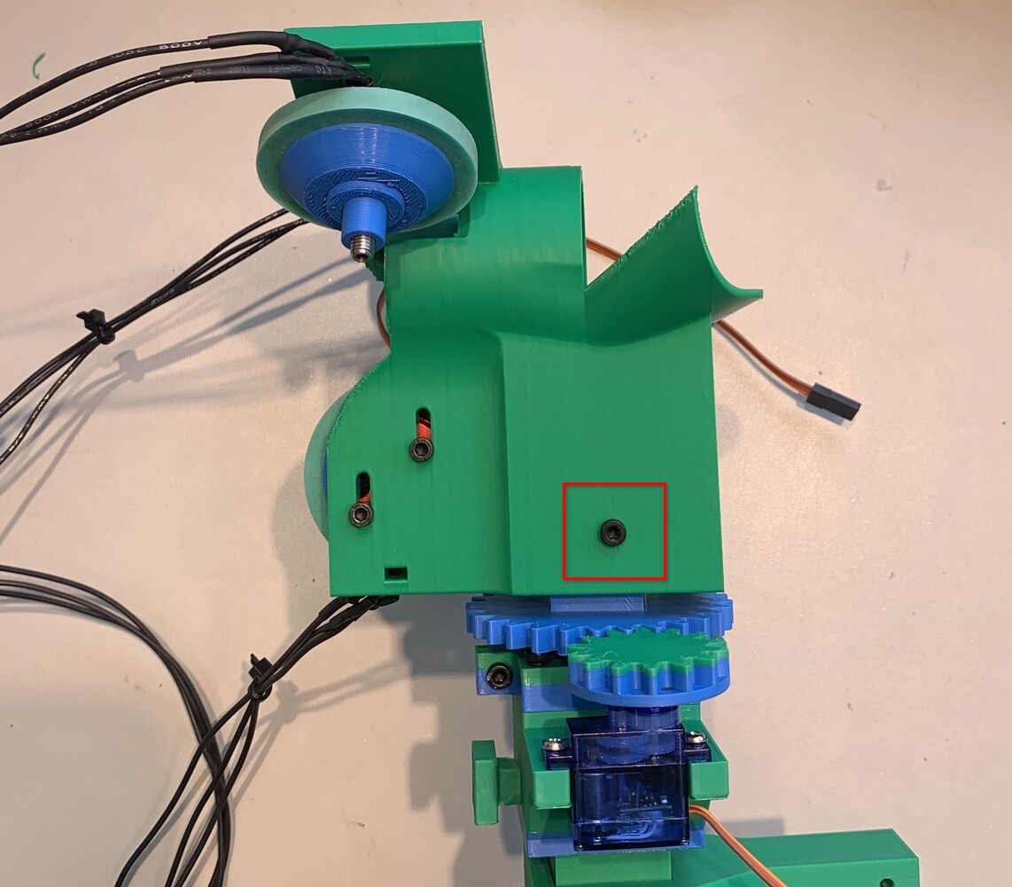
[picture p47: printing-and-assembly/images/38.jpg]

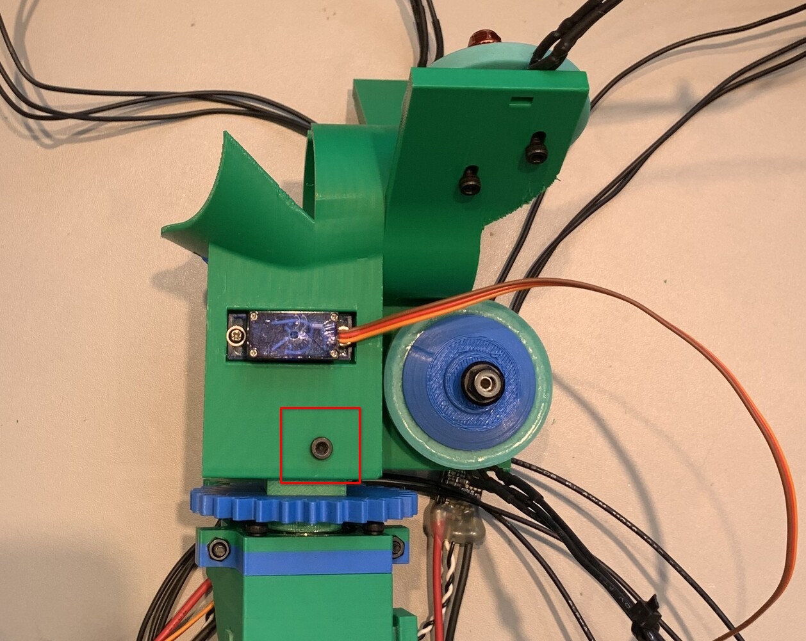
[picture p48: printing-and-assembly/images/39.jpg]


4. Secure the Pipe to the Fixture using four M3x12 bolts. Secure the Pipe to the Ball Pusher using two M3x8 bolts.

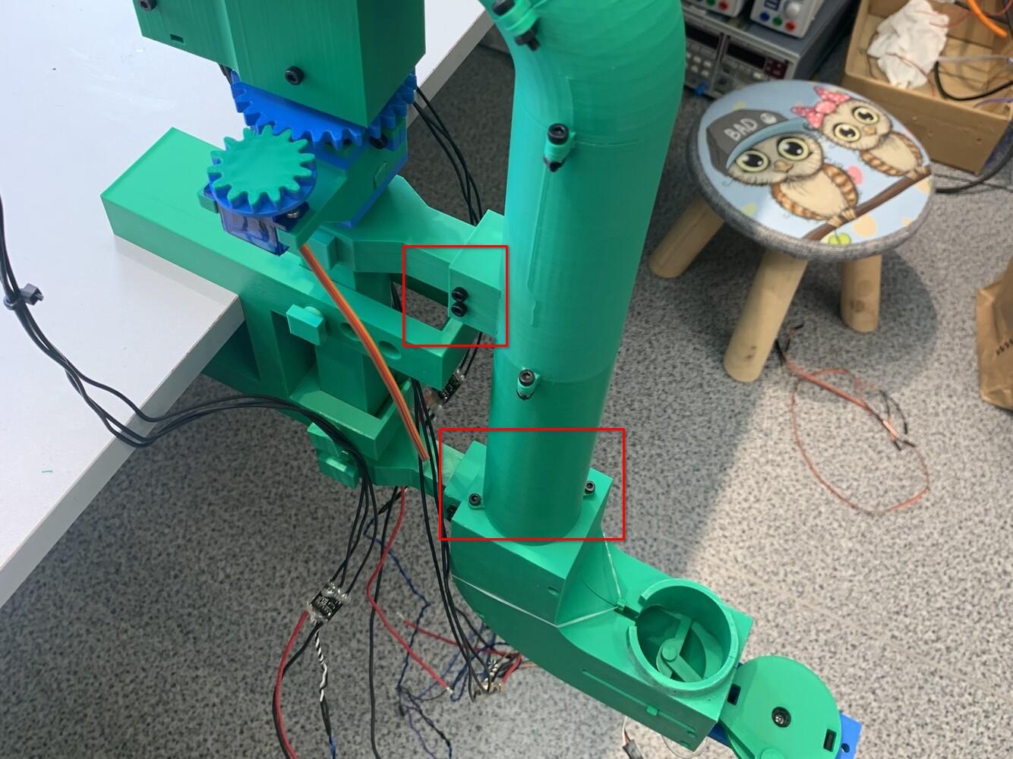
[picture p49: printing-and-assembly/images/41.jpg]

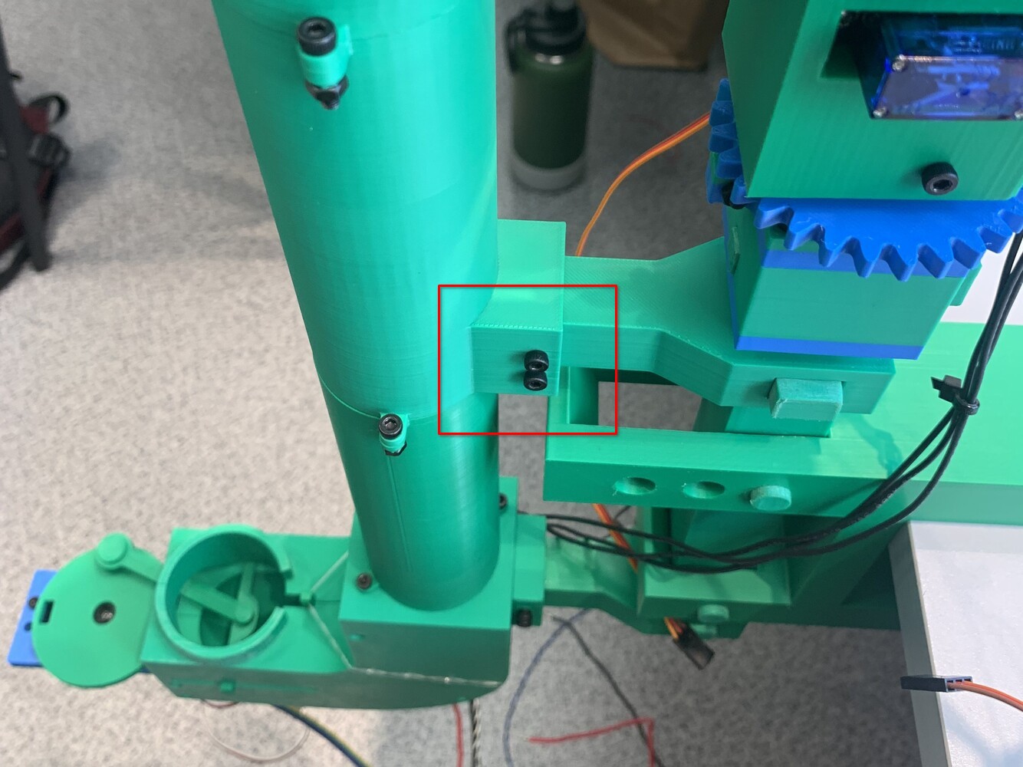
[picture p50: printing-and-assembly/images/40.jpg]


## Electronics

Hot glue the ESC's wires to prevent damage. I recommend also wrapping them using electrical tape.

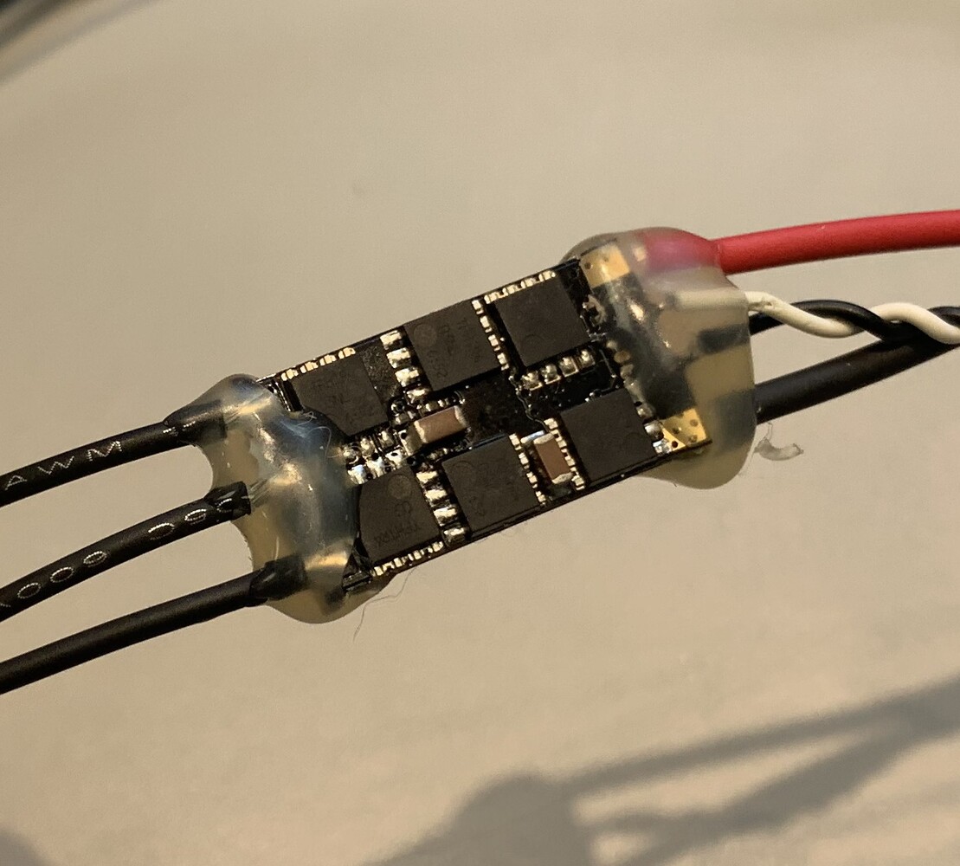
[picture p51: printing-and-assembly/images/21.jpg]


Connect the components according to the following schematic:

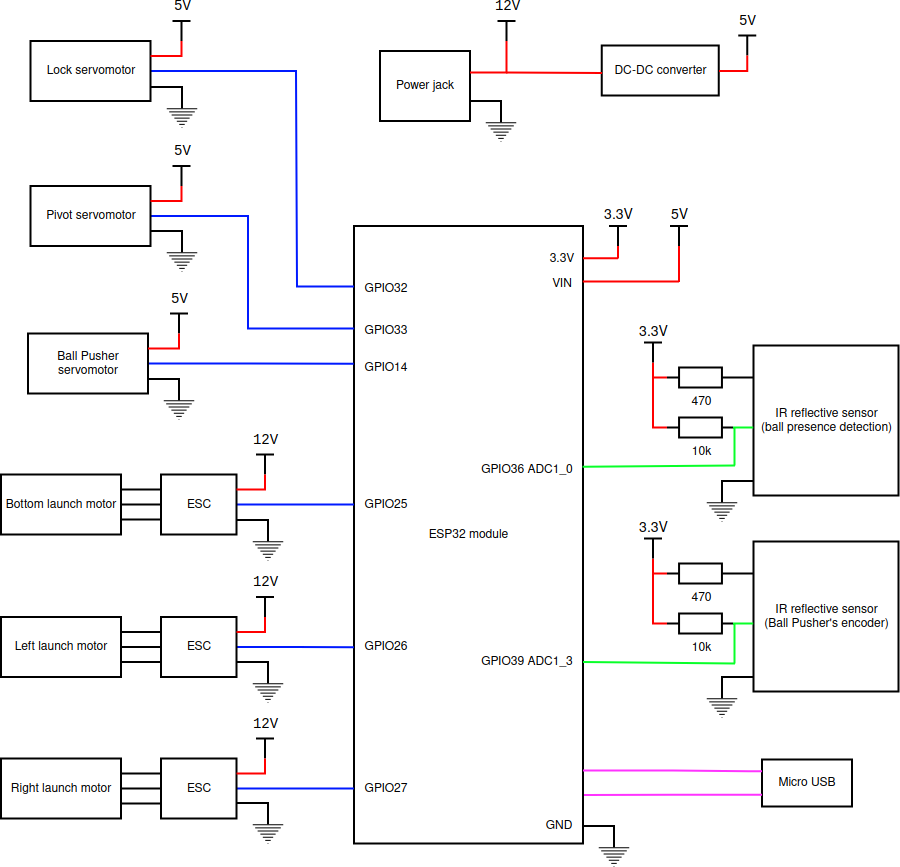
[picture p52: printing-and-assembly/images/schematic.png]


Although not strictly required I recommend using a protoboard for wiring the 5 V & 3.3 V power lines and for wiring the four resistors required by both IR reflective sensors.

The `Enclosure` can be used to house all the electronic components:

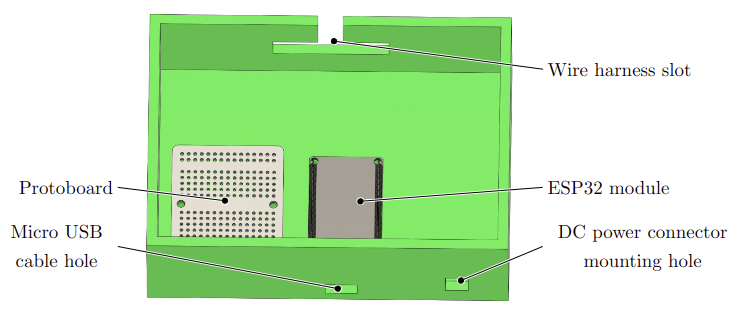
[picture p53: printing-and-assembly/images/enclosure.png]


The protoboard and ESP32 module are secured to the enclosure using 6 M3x8 bolts.

The different wirings can be tied together using cable ties and electrical tape to form a harness. Alternatively, sleeving or wire loom can be used.

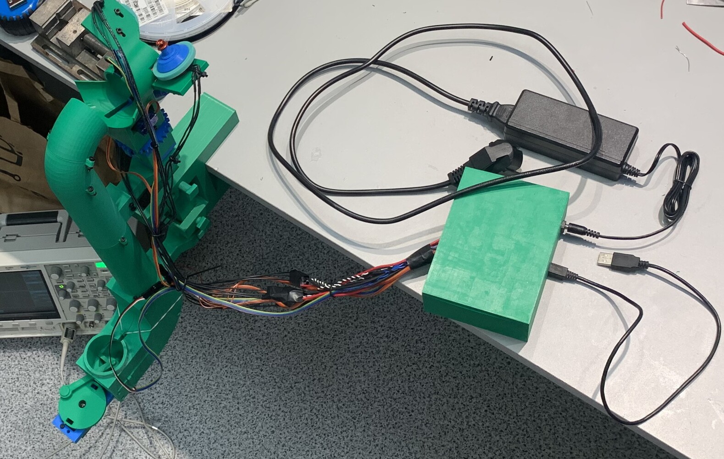
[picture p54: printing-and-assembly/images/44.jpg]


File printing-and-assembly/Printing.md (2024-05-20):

# Printing instructions

Models for printing are located in the subdirectories of `../models`. All models are orientated to their intended printing direction. All models are printed using PLA, a 0.4 mm nozzle, with 20% cubic infill and with 4 wall loops. Printing all the models (with supports) requires **1115 g** of filament.

`Rhea.step` contains the model of the whole assembly.

`Plates.3mf` contains organized build plates composed in BambuStudio:

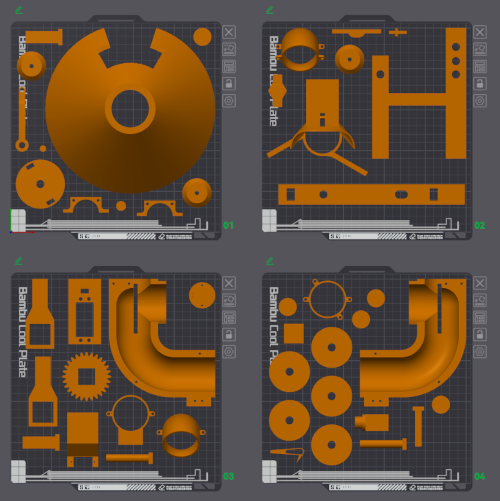
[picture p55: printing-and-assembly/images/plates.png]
plates


## Ball Pusher

Some smaller components can optionally be printed underneath the Funnel.

Component | Quantity | Supports required?
---|---|---
`Ball stopper.stl` | 1 | No
`Connecting rod.stl` | 1 | No
`Crank retaining pin.stl` | 1 | No
`Crank.stl` | 1 | Yes
`Funnel.stl` | 1 | Yes (only for the cantilever)
`Housing 1.stl` | 1 | Yes
`Housing 2.stl` | 1 | Yes
`Parallax servo holder.stl` | 1 | No
`Piston retaining pin.stl` | 1 | No
`Piston.stl` | 1 | Yes

## Pipe

Component | Quantity | Supports required?
---|---|---
`Angled connector pipe 1.stl` | 1 | Yes
`Angled connector pipe 2.stl` | 1 | Yes
`Straight connector pipe bottom.stl` | 1 | Yes
`Straight connector pipe top.stl` | 1 | Yes

## Launch Unit

Component | Quantity | Supports required?
---|---|---
`Launch Unit.stl` | 1 | Yes
`Motor guard.stl` | 3 | Yes
`Servo hook.stl` | 1 | No

## Traction wheel mould

Printing one of each part is sufficient but would require mulitple polysiloxane mixing sessions. The parts are quite small hence I recommend printing 3 of each.

Component | Quantity | Supports required?
---|---|---
`Traction wheel mould inner.stl` | 3 | No
`Traction wheel mould outer.stl` | 3 | No

## Pivot Mechanism

Component | Quantity | Supports required?
---|---|---
`Bearing housing.stl` | 2 | No
`Driven gear.stl` | 1 | No
`Driver gear.stl` | 1 | No
`Housing.stl` | 1 | Yes
`Shaft.stl` | 1 | Yes

## Fixture

Component | Quantity | Supports required?
---|---|---
`Bolt pad.stl` | 1 | No
`Bolt.stl` | 1 | No
`Clamp.stl` | 1 | Yes
`Pusher and Pipe connector.stl` | 2 | Yes
`Rectangular dowel.stl` | 2 | Yes
`Rod.stl` | 1 | No
`Round dowel.stl` | 2 | Yes
`Square dowel.stl` | 1 | Yes

## Electronics enclosure

Component | Quantity | Supports required?
---|---|---
`Enclosure lid.stl` | 1 | No
`Enclosure.stl` | 1 | No

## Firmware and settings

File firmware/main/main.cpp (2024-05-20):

#include <stdio.h>
#include <string.h>
#include <inttypes.h>

#include "freertos/FreeRTOS.h"
#include "freertos/task.h"
#include "freertos/queue.h"
#include "freertos/semphr.h"

#include <driver/uart.h>
#include <esp_log.h>

#include "UART.hpp"
#include "PWMMotors.hpp"
#include "IRSensors.hpp"
#include "StateMachine.hpp"

constexpr const char* TAG = "main";

constexpr auto UART_NUM = UART_NUM_0;
constexpr auto UART_PIN = UART_PIN_NO_CHANGE;

constexpr auto UART_BUFFER_SIZE = 1024;

extern "C"
void app_main(void) {
    UART::Init(StateMachine::ProcessPacket);
    PWMMotors::Init();
    IRSensors::Init();
    StateMachine::Init();

    // Get Ball Pusher to an initial "good" state.
    vTaskDelay(10 / portTICK_PERIOD_MS);
    if (!IRSensors::IsBallDetected()) {
        IRSensors::StartPushingBall();
    }
}

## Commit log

2024-05-20 Add files.
    [Angled connector pipe 1.stl, Angled connector pipe 2.stl, Ball stopper.stl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]
2024-05-20 Add bom.
